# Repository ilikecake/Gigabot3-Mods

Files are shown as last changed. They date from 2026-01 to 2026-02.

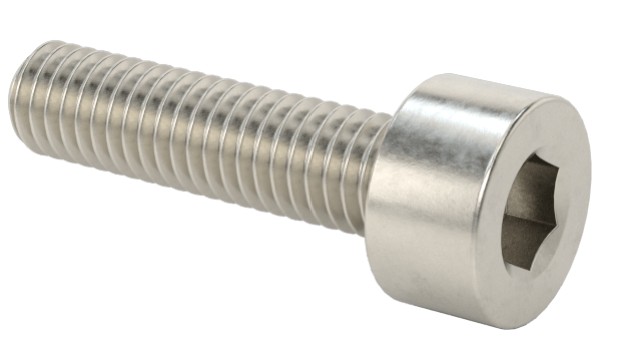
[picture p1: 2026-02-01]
Optical Endstop/M3_SHCS.jpg

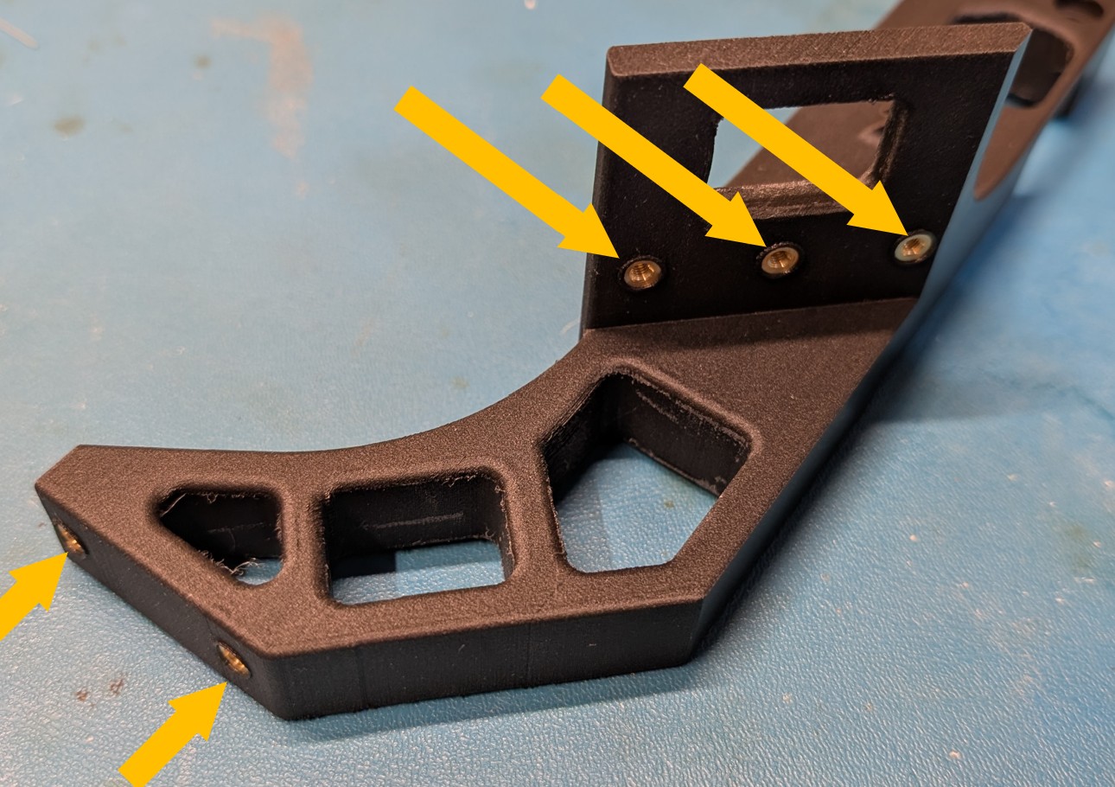
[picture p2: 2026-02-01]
XY Upright/Install_heatset.jpg

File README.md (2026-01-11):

# Gigabot 3 Mods
This repo is here to document modifications I made to the Gigabot XLT 3+. More details on the mods can be found in the Wiki.

## Background

My work purchased this [Gigabot XLT 3+](https://shop.re3d.org/pages/gigabot-xlt-3-tech-specs) a while back, looking for large format printing capability. While we did get some good prints from this printer, I found it to be pretty unreliable. As time went on, it got worse and for the last few years, it has been sitting broken in the basement of my workplace. They eventually decided to cut their losses and get rid of the printer, so I took it home. This repo documents my efforts to get the printer running again and hopefully fix some of the issues we found.

## Wishlist

Here is a list of the various things I hope to do with this printer.

Required:
- [x] Get the printer running with an upgraded firmware.
- [ ] Add a bed sensor for auto bed leveling.
- [ ] Replace the X and Y motor mounts with machined versions.
- [ ] Rebuild the print head.
- [ ] Move the thermocouple amplifier for the bed thermocouple to avoid interference with the AC bed heater.

Optional:
- [ ] Update Y endstops to optical sensors.
- [ ] Replace motor drivers with more modern variants.

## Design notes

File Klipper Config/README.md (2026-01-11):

# Klipper configuration files

 - base-config.cfg:		A basic klipper configuration that should work with the stock Gigabot XLT 3+.

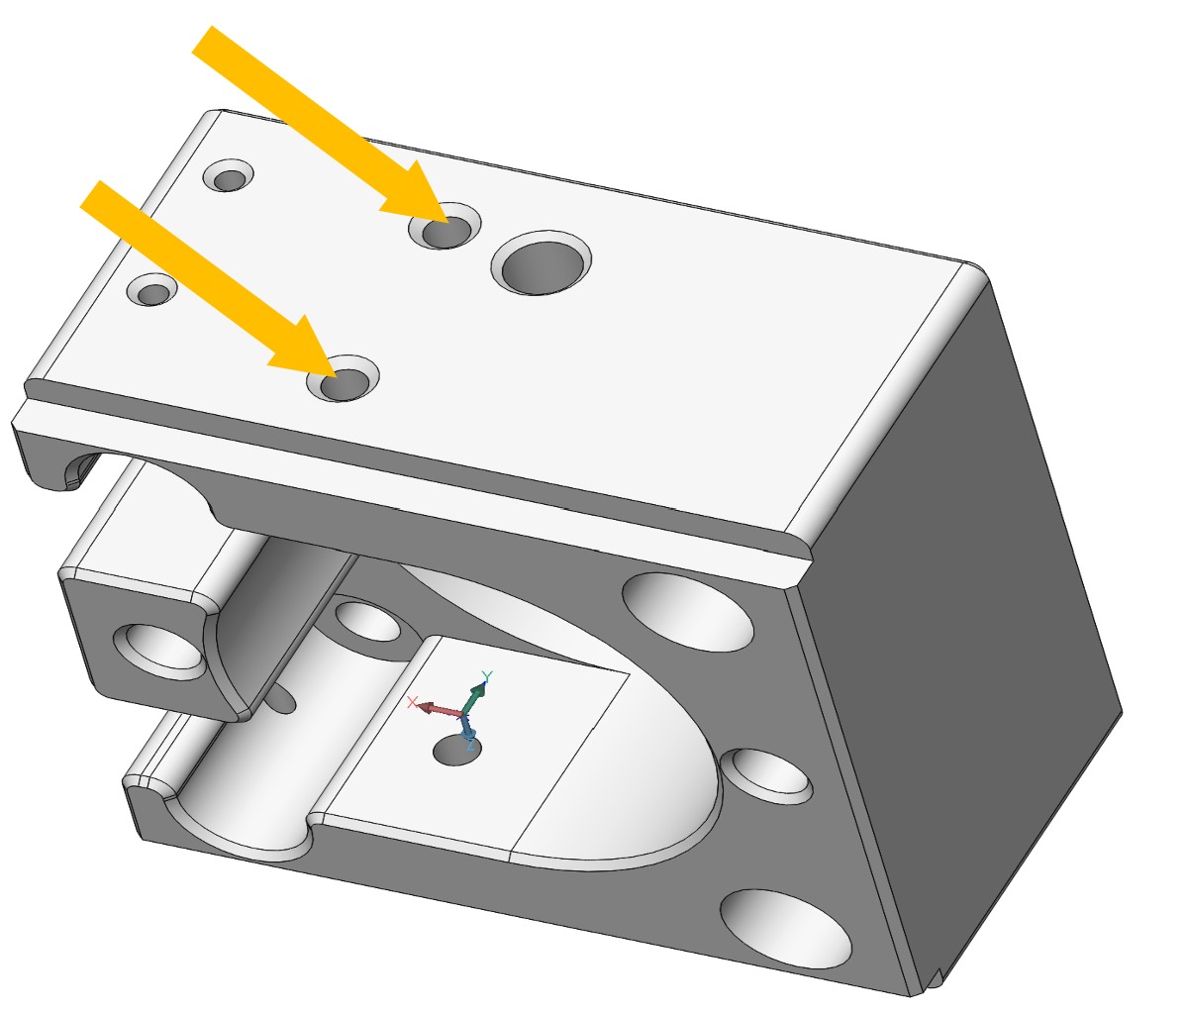
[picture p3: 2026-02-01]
Optical Endstop/Motor_mount_tap_M3.jpg

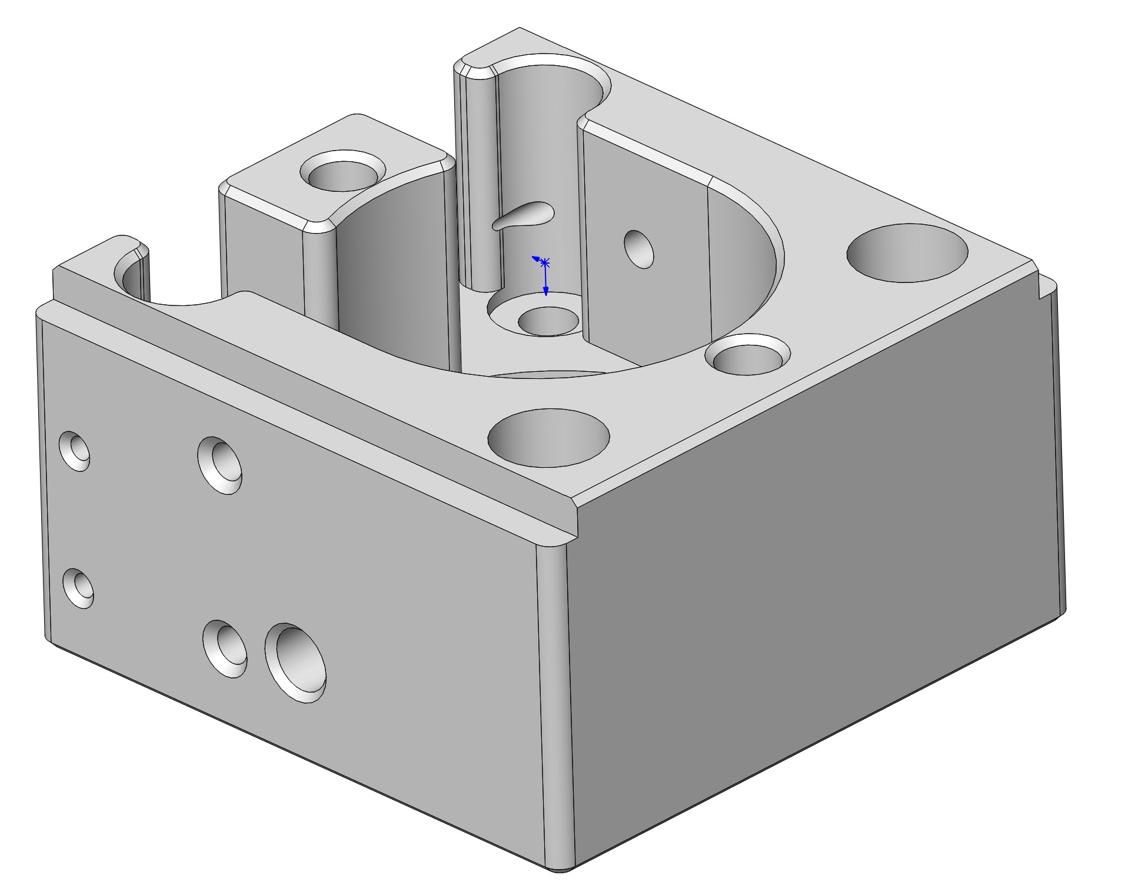
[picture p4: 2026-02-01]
Optical Endstop/Motor_mount_cad.jpg

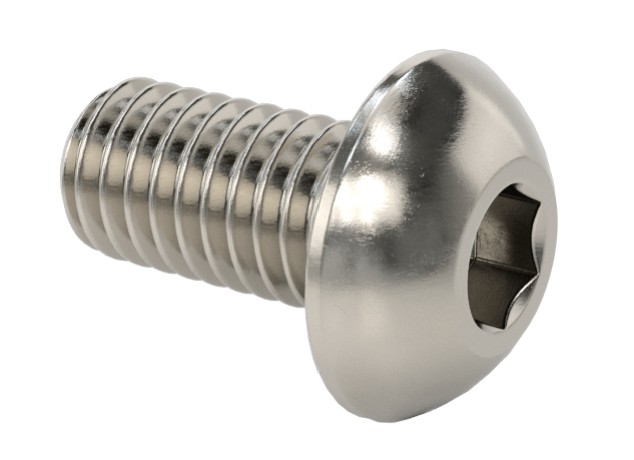
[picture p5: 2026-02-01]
Optical Endstop/M3_BHCS.jpg

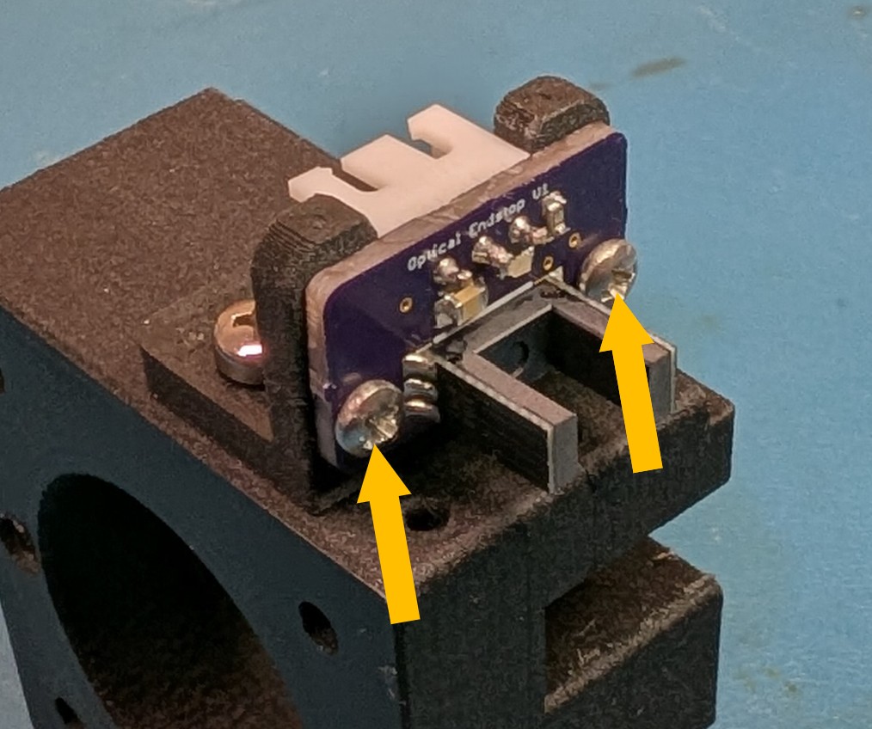
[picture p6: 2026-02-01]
Optical Endstop/PCB_to_mount.jpg

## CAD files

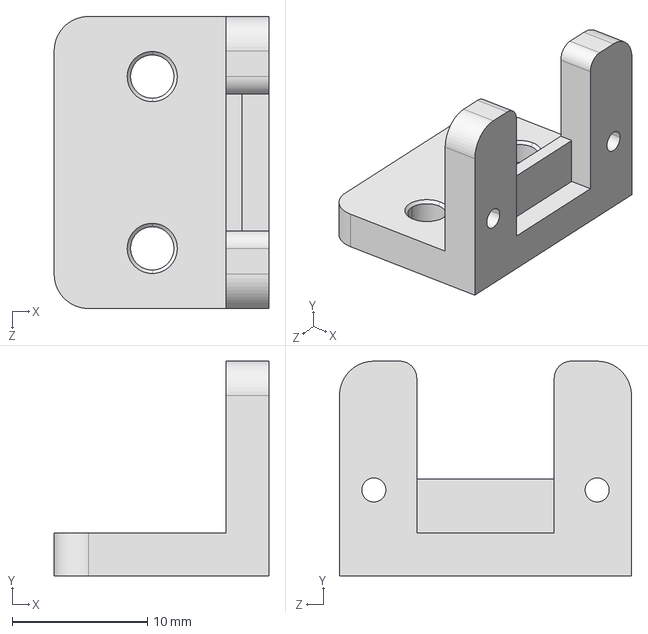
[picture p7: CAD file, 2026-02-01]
Optical Endstop/XY Optical Endstop Mount.STEP
15.9 x 15.9 x 21.6 mm

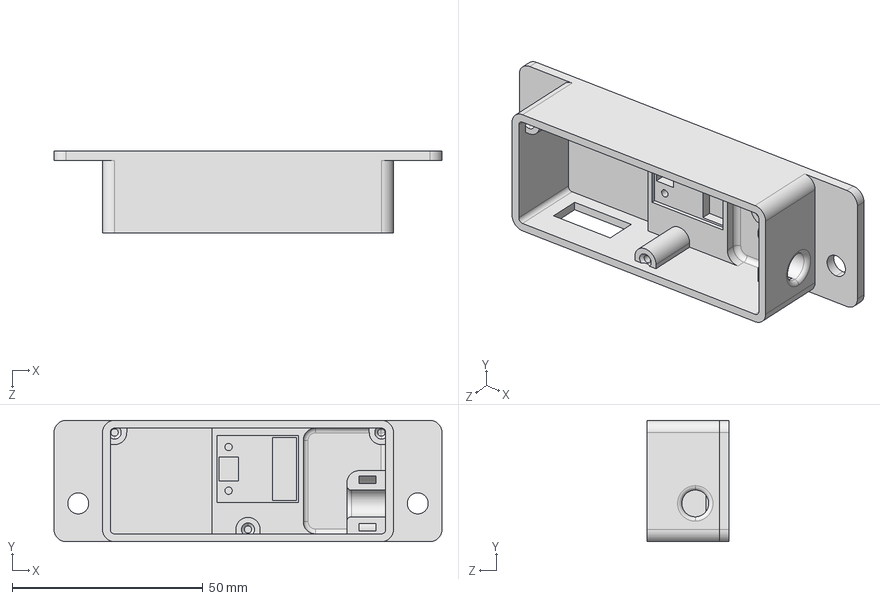
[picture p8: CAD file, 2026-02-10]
Thermocouple Amp/Thermocouple Conditioner Case.STEP
101.6 x 31.8 x 21.6 mm

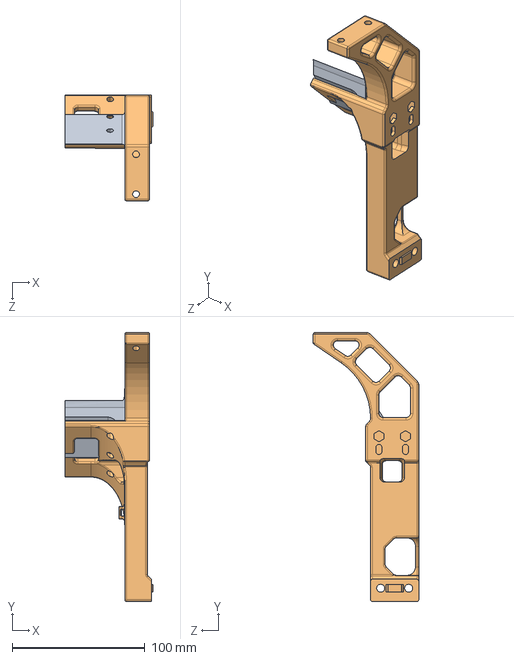
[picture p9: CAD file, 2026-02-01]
XY Upright/GB3+ XY Upright - Modified.STEP
66.3 x 202.5 x 79.5 mm

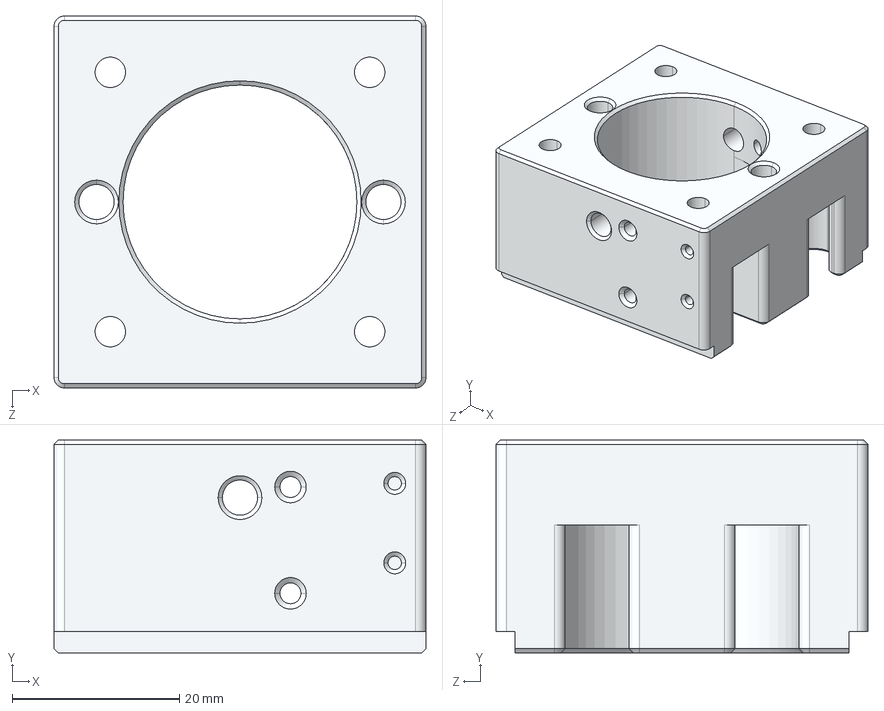
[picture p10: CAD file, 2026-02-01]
Optical Endstop/Motor Mount - Modified.STEP
44.4 x 25.4 x 44.5 mm

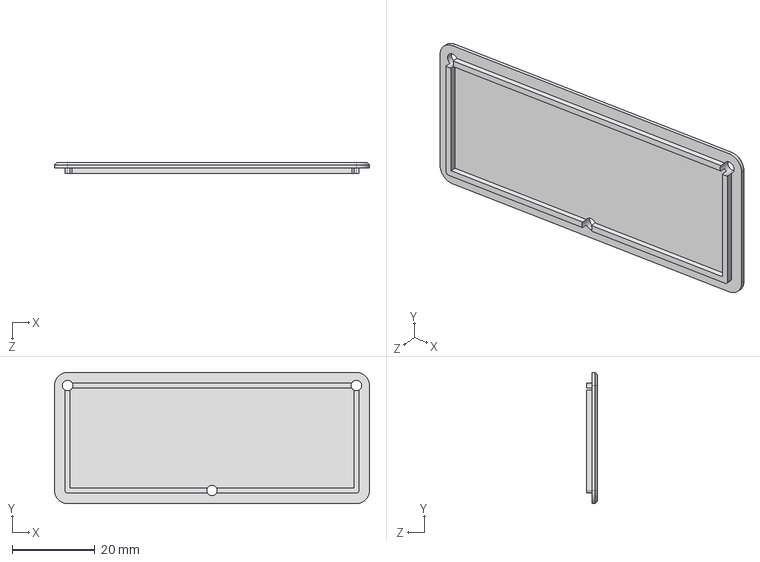
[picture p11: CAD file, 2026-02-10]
Thermocouple Amp/Thermocouple Conditioner Case Top.STEP
76.2 x 31.8 x 2.54 mm

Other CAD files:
Optical Endstop/Motor Mount - Modified.SLDPRT
Optical Endstop/Motor Mount - Modified.STL
Optical Endstop/XY Optical Endstop Mount.SLDPRT
Optical Endstop/XY Optical Endstop Mount.STL
Thermocouple Amp/Thermocouple Conditioner Case Top.SLDPRT
Thermocouple Amp/Thermocouple Conditioner Case Top.STL
Thermocouple Amp/Thermocouple Conditioner Case.SLDPRT
Thermocouple Amp/Thermocouple Conditioner Case.STL
XY Upright/GB3+ XY Upright - Modified.SLDPRT

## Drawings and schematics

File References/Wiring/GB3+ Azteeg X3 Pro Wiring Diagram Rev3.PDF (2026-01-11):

# + AZTEEG

# + ELECTRICAL BOX FANS

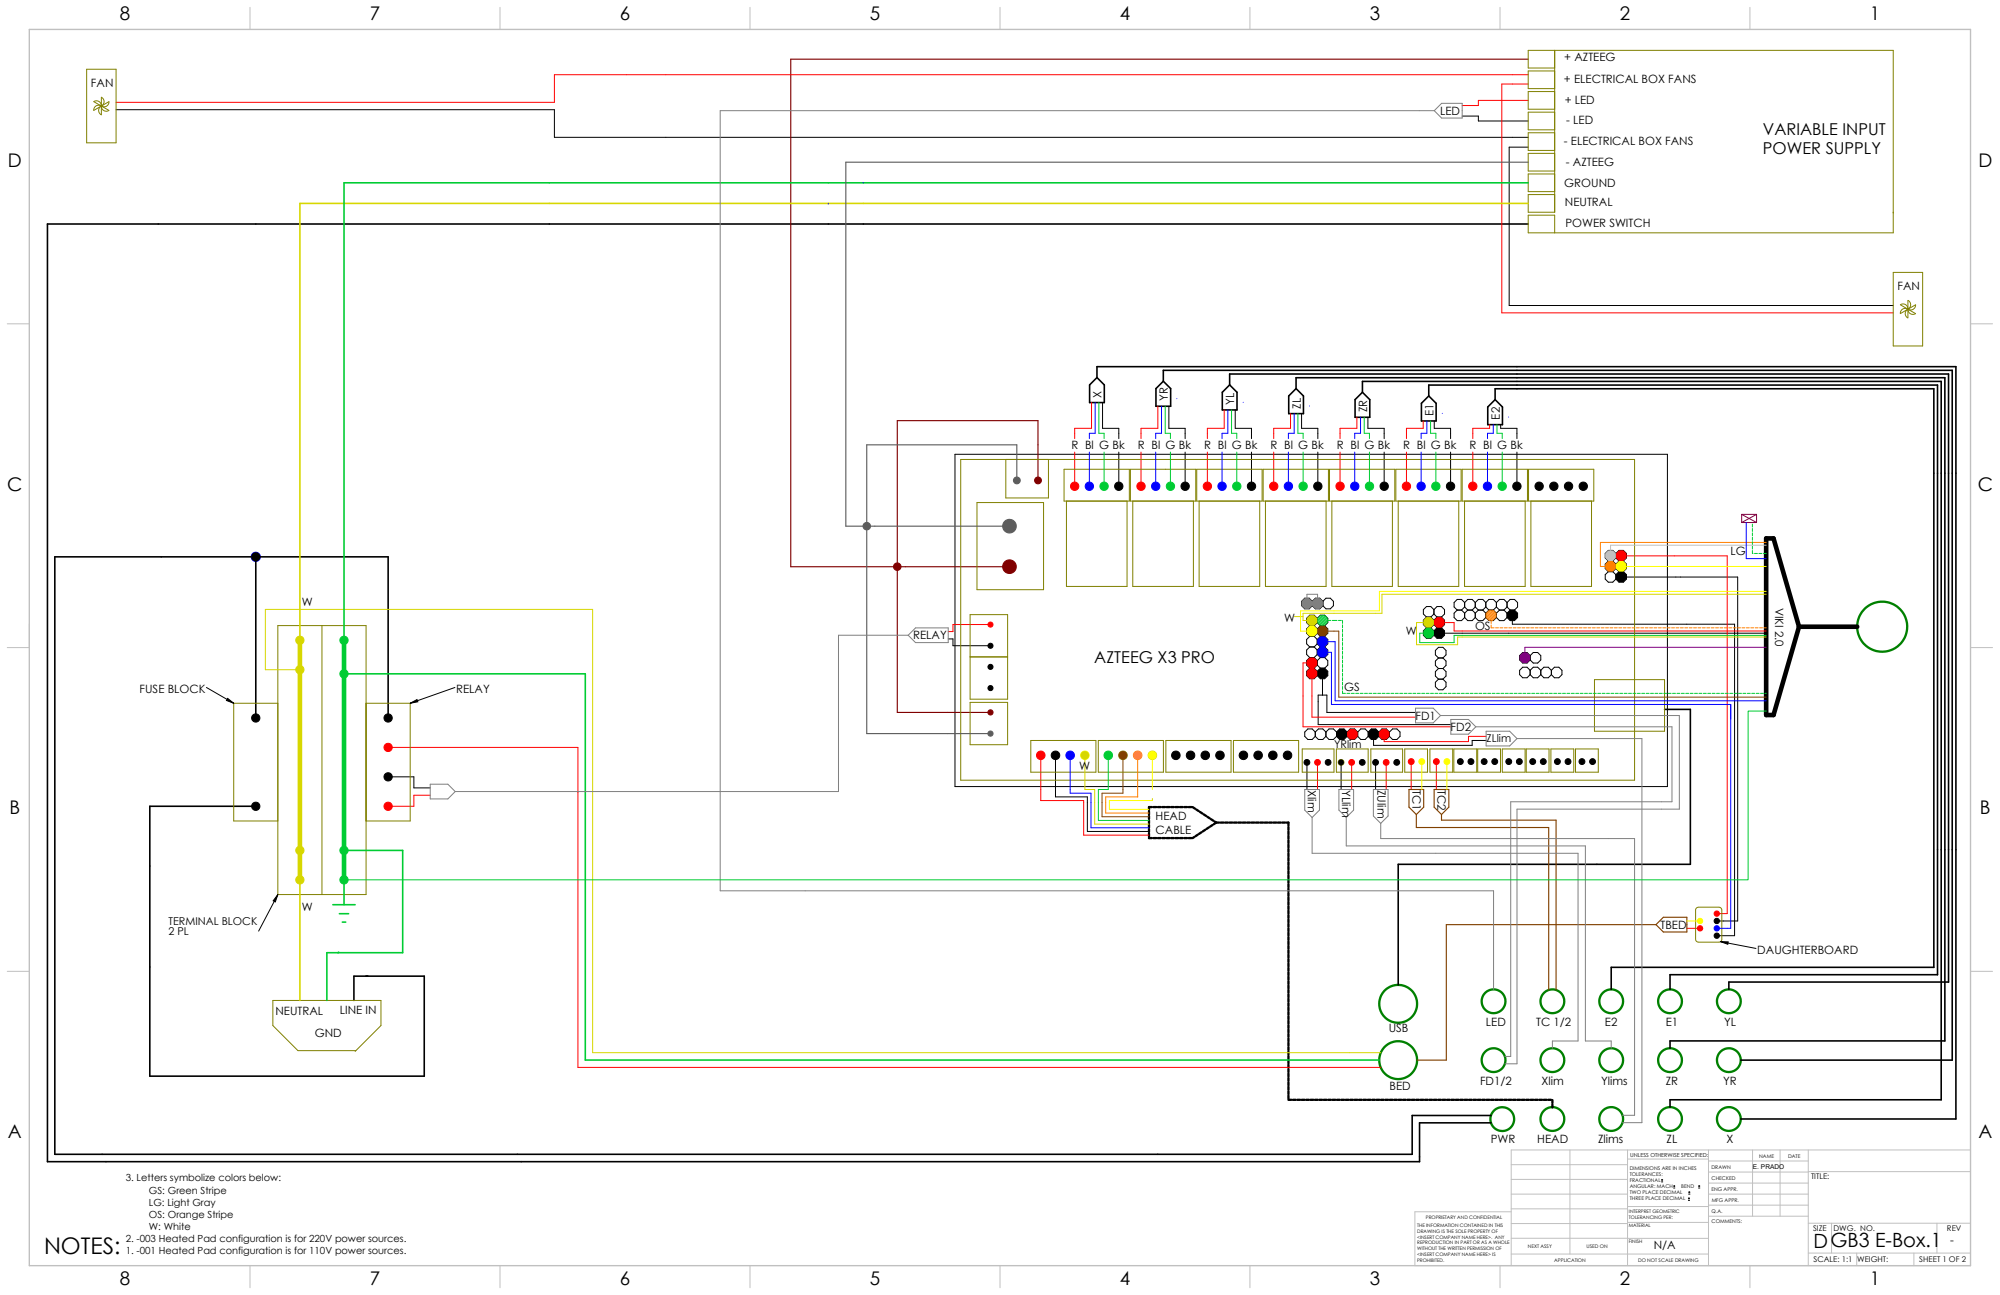
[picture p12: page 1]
HEAD; USB; BED; PWR; LED; Zlims; Xlim; Ylims; Ulim; ZLlim; + LED - LED; - ELECTRICAL BOX FANS; - AZTEEG; GROUND NEUTRAL; POWER SWITCH; GND; LINE IN; FAN; VIKI 2.0; HEAD CABLE; Llim; FUSE BLOCK; RELAY; VARIABLE INPUT POWER SUPPLY; AZTEEG X3 PRO; TERMINAL BLOCK 2 PL; TBED; DAUGHTERBOARD; NEUTRAL; NOTES:; YRlim; COMMENTS:

UNLESS OTHERWISE SPECIFIED: | | NAME | DATE
DIMENSIONS ARE IN INCHES TOLERANCES: FRACTIONAL ANGULAR: MACH BEND TWO PLACE DECIMAL THREE PLACE DECIMAL | DRAWN | E. PRADO

3. Letters symbolize colors below:
GS: Green Stripe
LG: Light Gray
OS: Orange Stripe
W: White
2. -003 Heated Pad configuration is for 220V power sources.
1. -001 Heated Pad configuration is for 110V power sources.

CHECKED | | | TITLE:

ENG APPR.
MFG APPR.

INTERPRET GEOMETRIC TOLERANCING PER: | Q.A.
MATERIAL | | SIZE D | DWG. NO. GB3 E-Box.1 | REV -

PROPRIETARY AND CONFIDENTIAL
THE INFORMATION CONTAINED IN THIS
DRAWING IS THE SOLE PROPERTY OF
<INSERT COMPANY NAME HERE>. ANY
REPRODUCTION IN PART OR AS A WHOLE
WITHOUT THE WRITTEN PERMISSION OF
<INSERT COMPANY NAME HERE> IS
PROHIBITED.

NEXT ASSY | USED ON | FINISH N/A

APPLICATION | DO NOT SCALE DRAWING | | SCALE: 1:1 | WEIGHT: | SHEET 1 OF 2

YL

E2 | E1

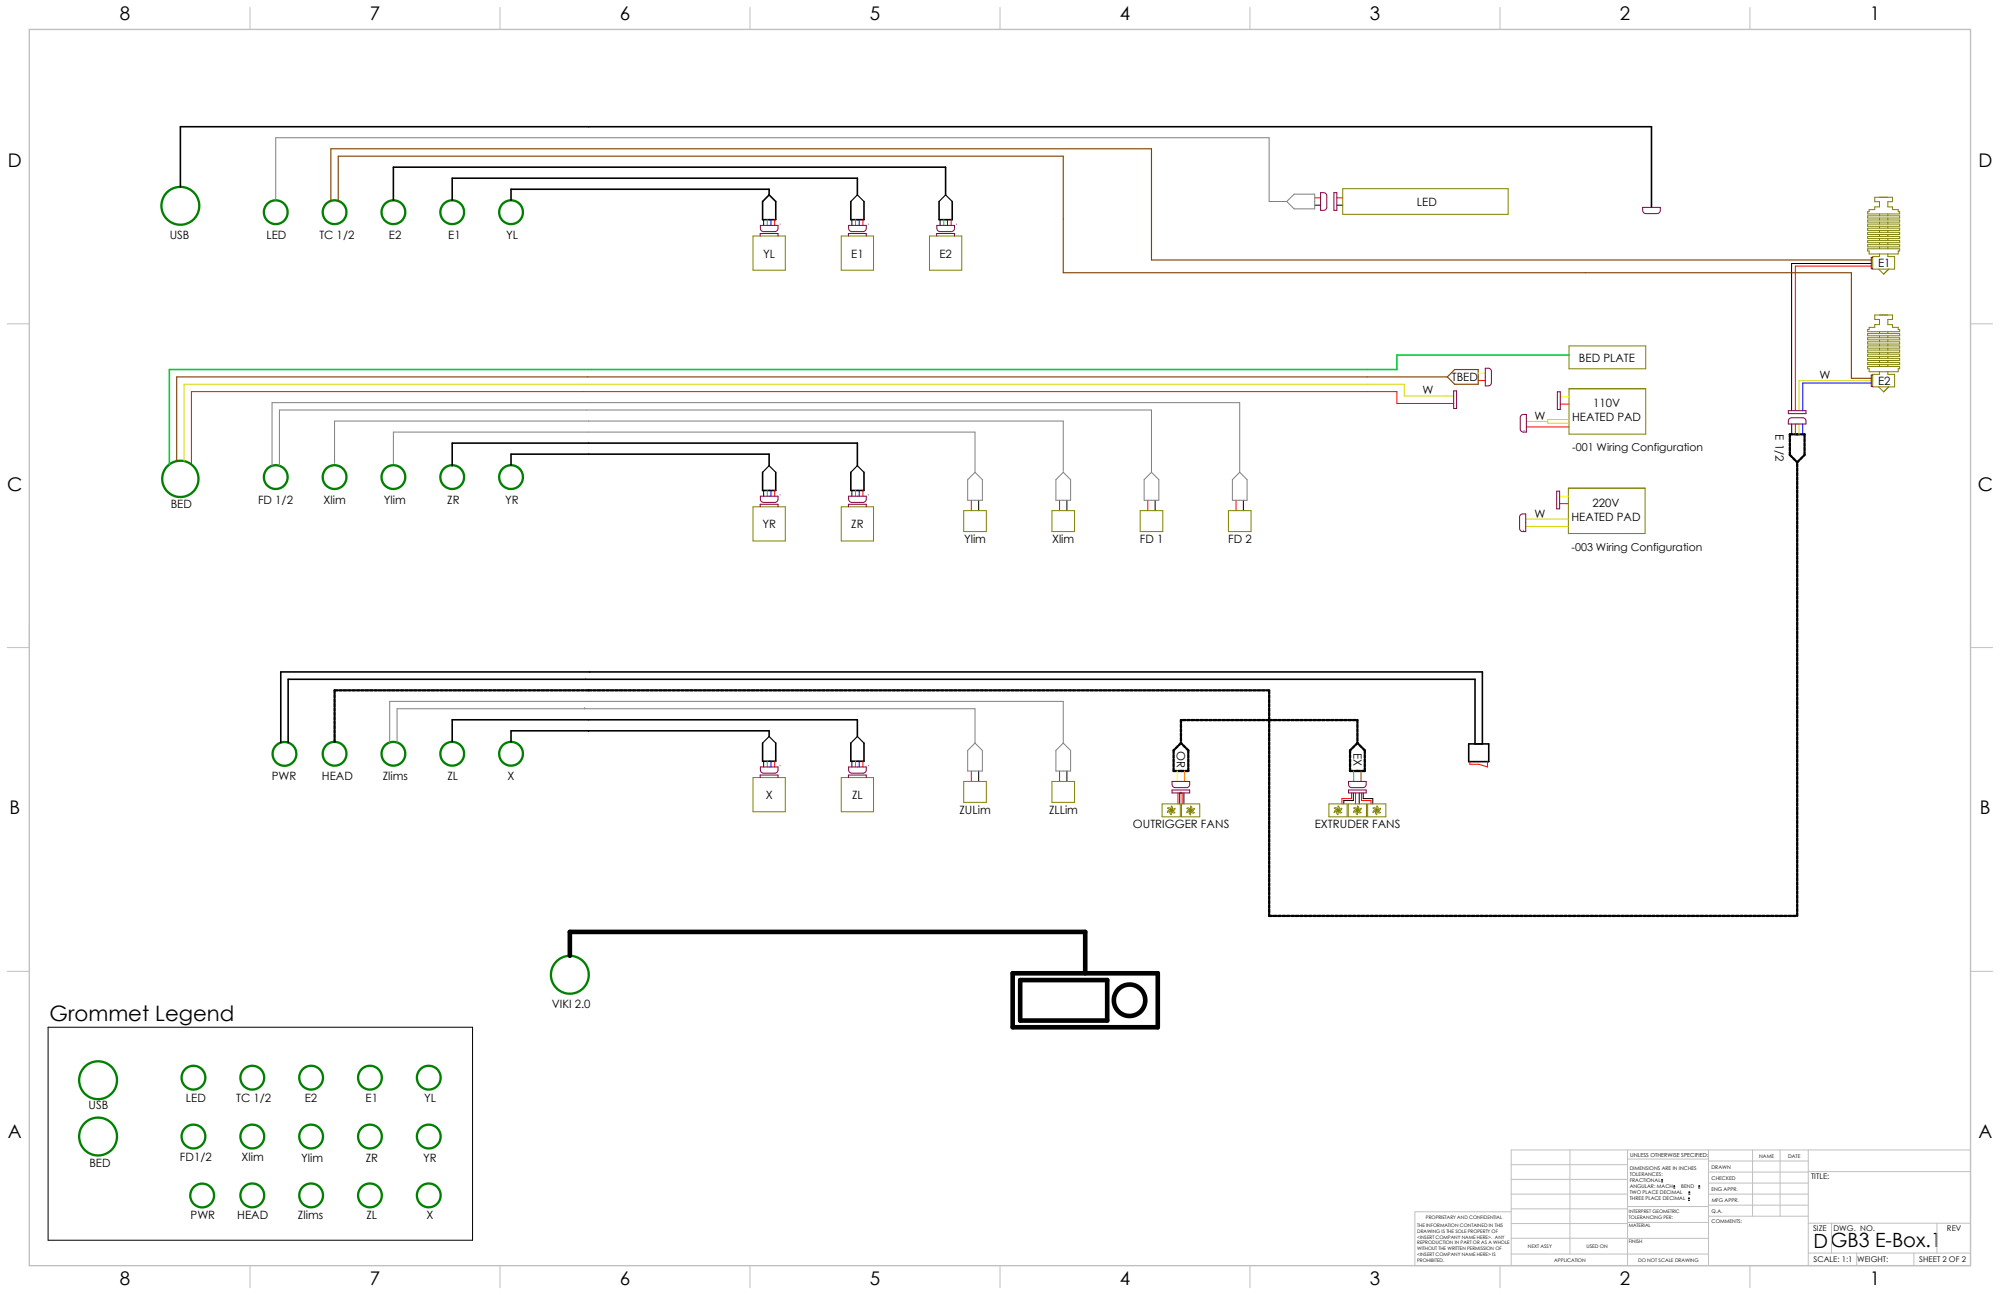
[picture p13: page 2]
HEAD; ZR BED; USB; PWR; LED; Zlims; Xlim; Ylim; BED PLATE; 110V HEATED PAD; VIKI 2.0; OUTRIGGER FANS; EXTRUDER FANS; ZULim; ZLLim; TBED; 220V HEATED PAD; -001 Wiring Configuration; -003 Wiring Configuration; BED; Grommet Legend; COMMENTS:

UNLESS OTHERWISE SPECIFIED: | | NAME | DATE

DIMENSIONS ARE IN INCHES TOLERANCES: FRACTIONAL ANGULAR: MACH BEND TWO PLACE DECIMAL THREE PLACE DECIMAL | DRAWN

CHECKED | | | TITLE:

ENG APPR.
MFG APPR.

INTERPRET GEOMETRIC TOLERANCING PER: | Q.A.
MATERIAL | | SIZE D | DWG. NO. GB3 E-Box.1 | REV

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

NEXT ASSY | USED ON | FINISH

APPLICATION | DO NOT SCALE DRAWING | | SCALE: 1:1 | WEIGHT: | SHEET 2 OF 2

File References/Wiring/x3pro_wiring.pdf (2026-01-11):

### X-AXIS Y-AXIS Z-AXIS EXTR1

## STEPPER MOTORS

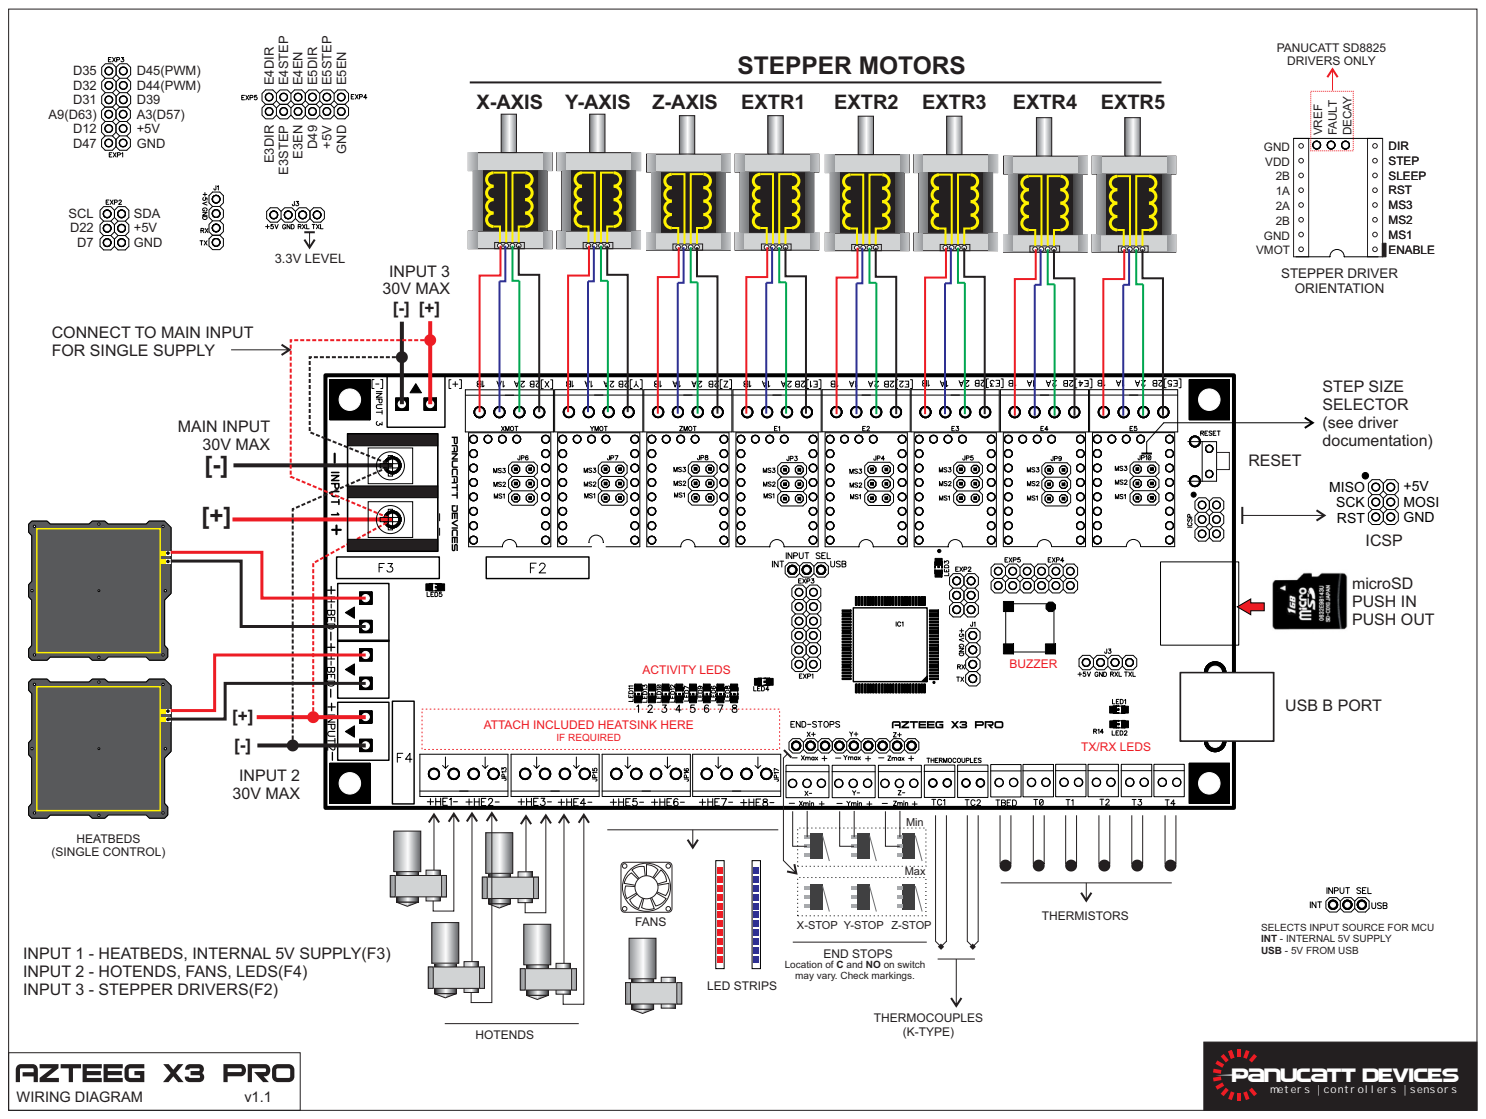
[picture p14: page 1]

CONNECT TO MAIN INPUT
FOR SINGLE SUPPLY

ATTACH INCLUDED HEATSINK HERE

SELECTS INPUT SOURCE FOR MCU
INT - INTERNAL 5V SUPPLY
USB - 5V FROM USB

INPUT 1 - HEATBEDS, INTERNAL 5V SUPPLY(F3)
INPUT 2 - HOTENDS, FANS, LEDS(F4)
INPUT 3 - STEPPER DRIVERS(F2)

Location of C and NO on switch
may vary. Check markings.

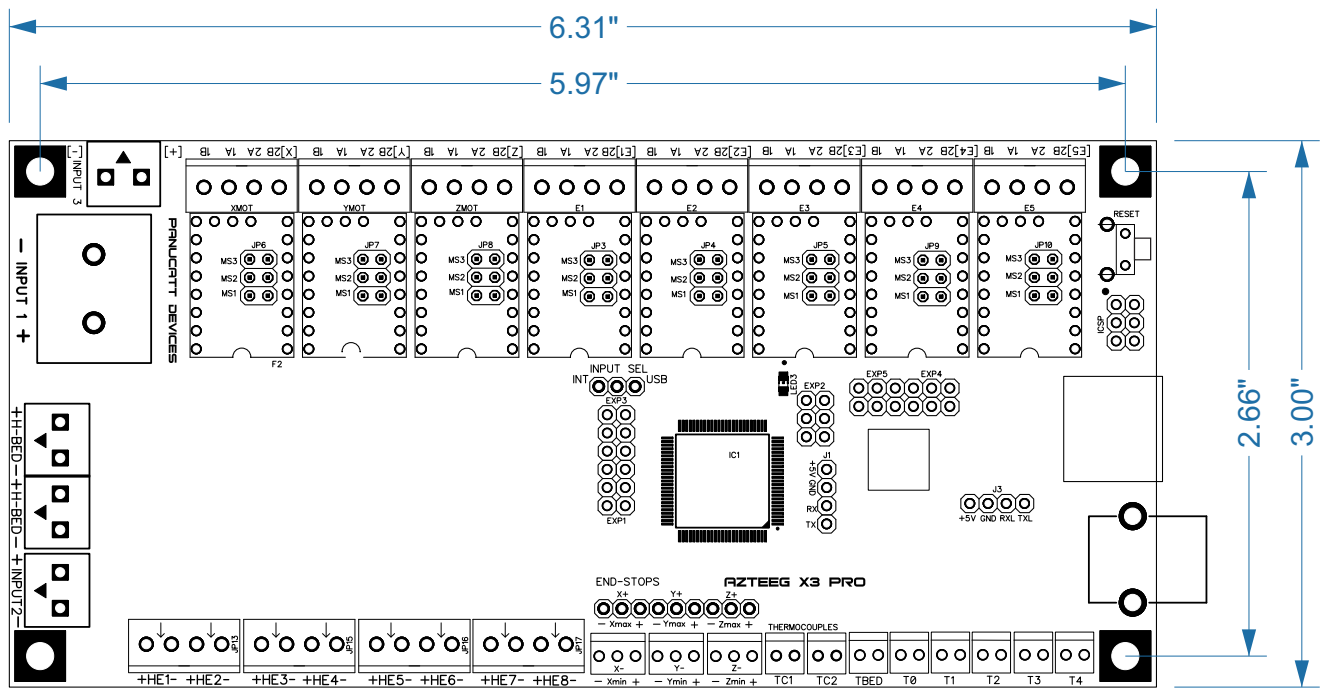
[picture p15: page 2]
WIRING DIAGRAM; PANUCATT DEVICES

meters | controllers | sensors

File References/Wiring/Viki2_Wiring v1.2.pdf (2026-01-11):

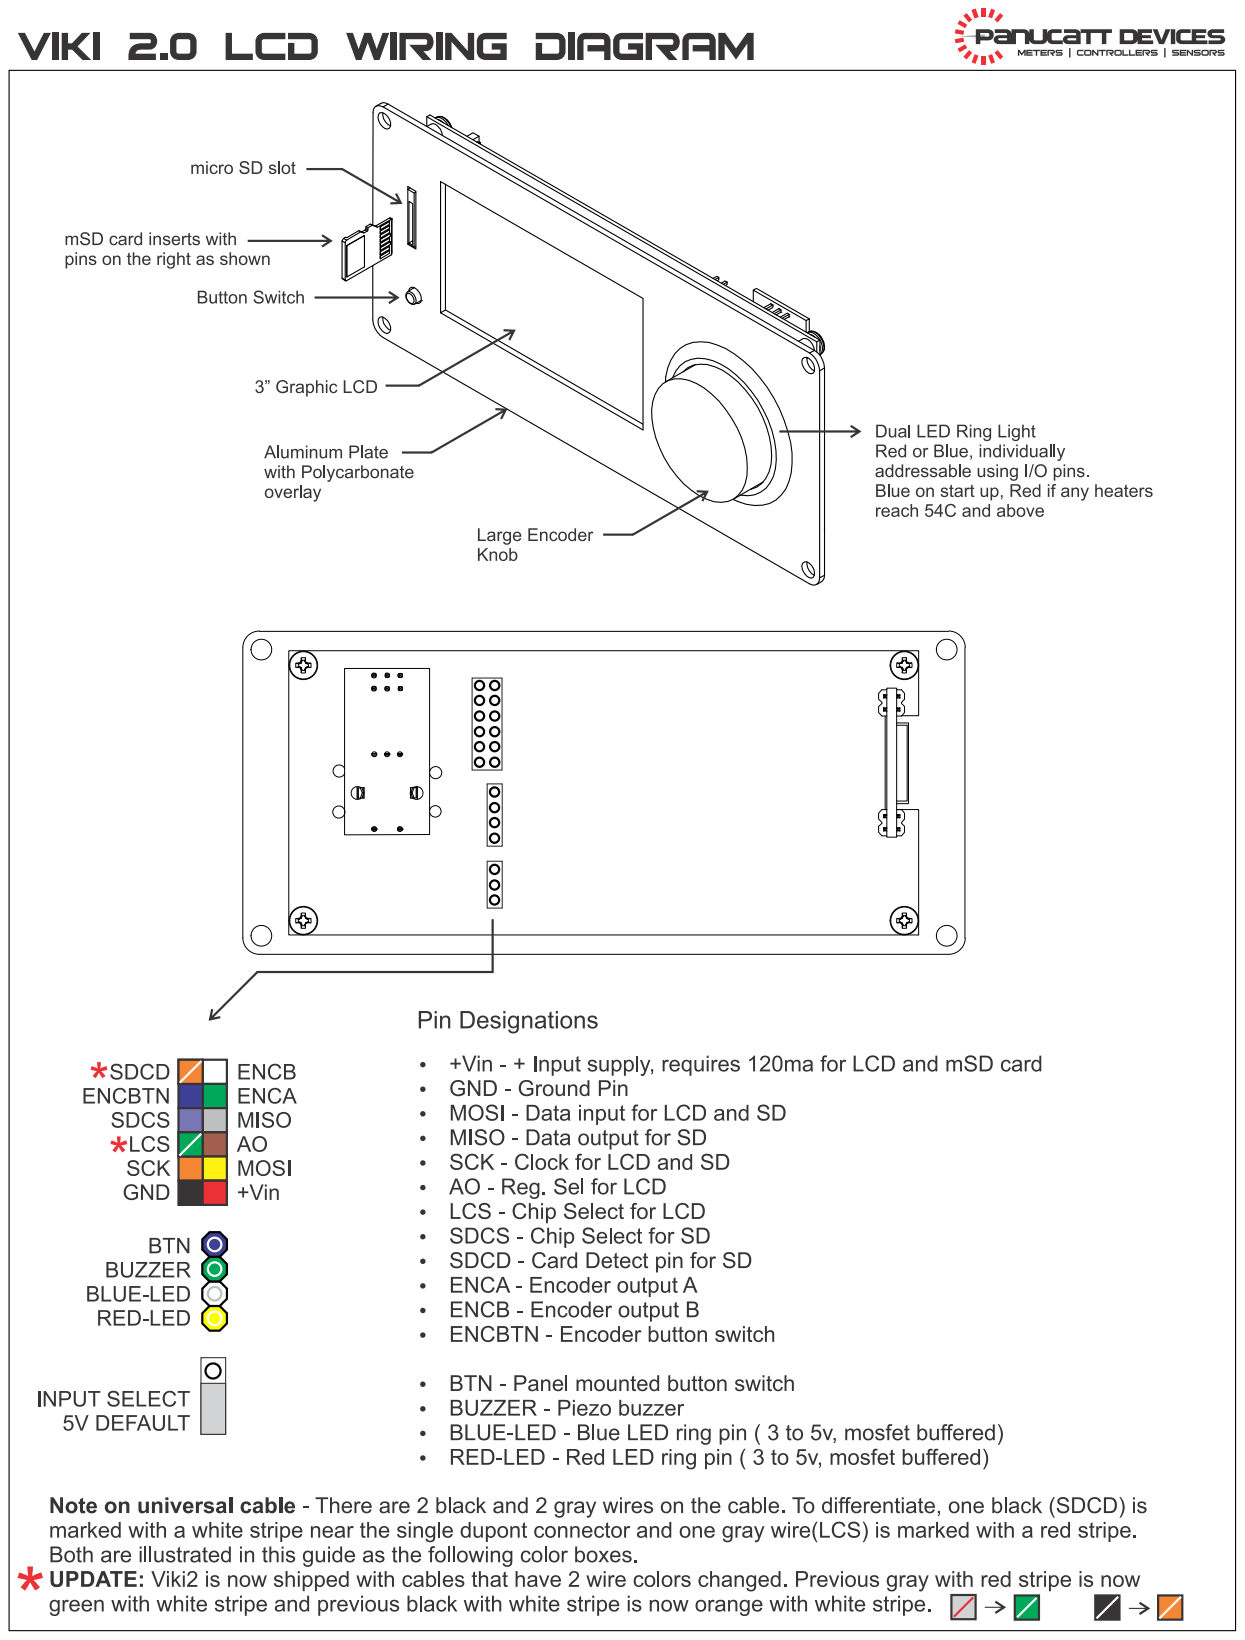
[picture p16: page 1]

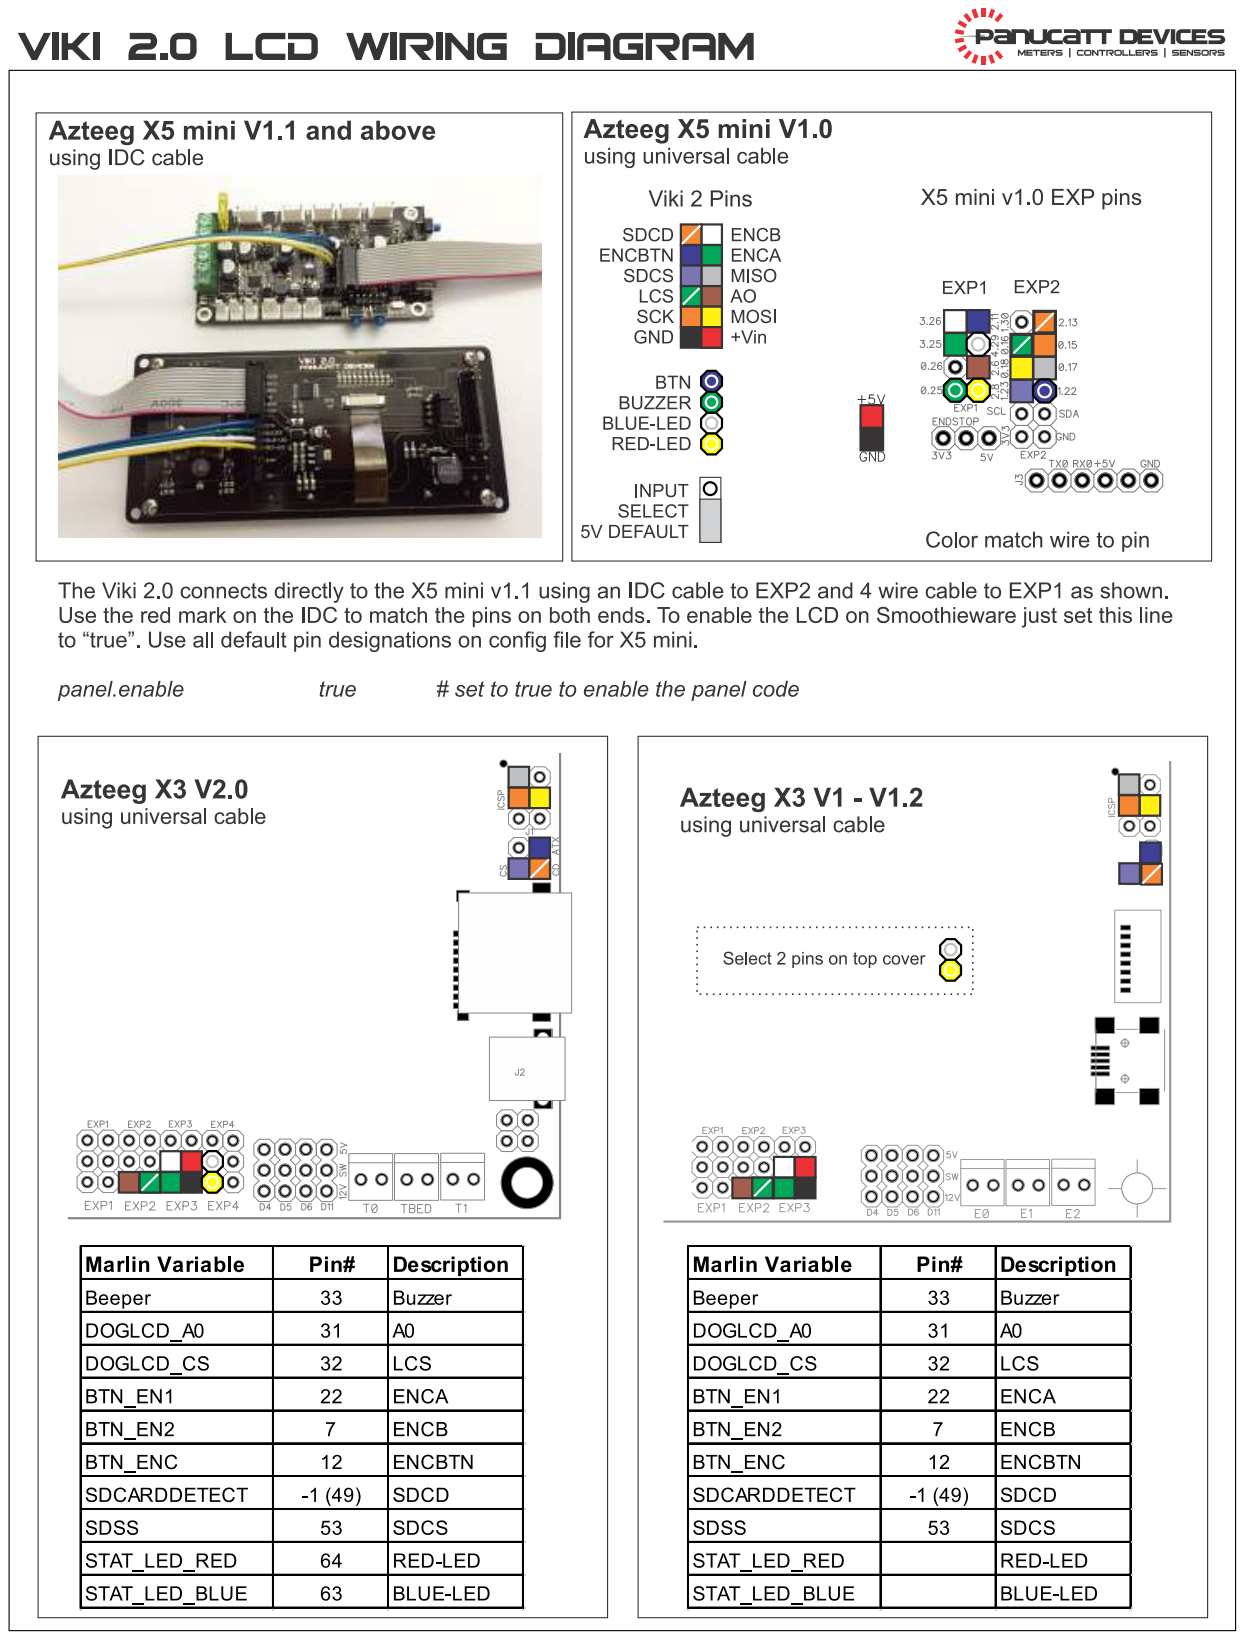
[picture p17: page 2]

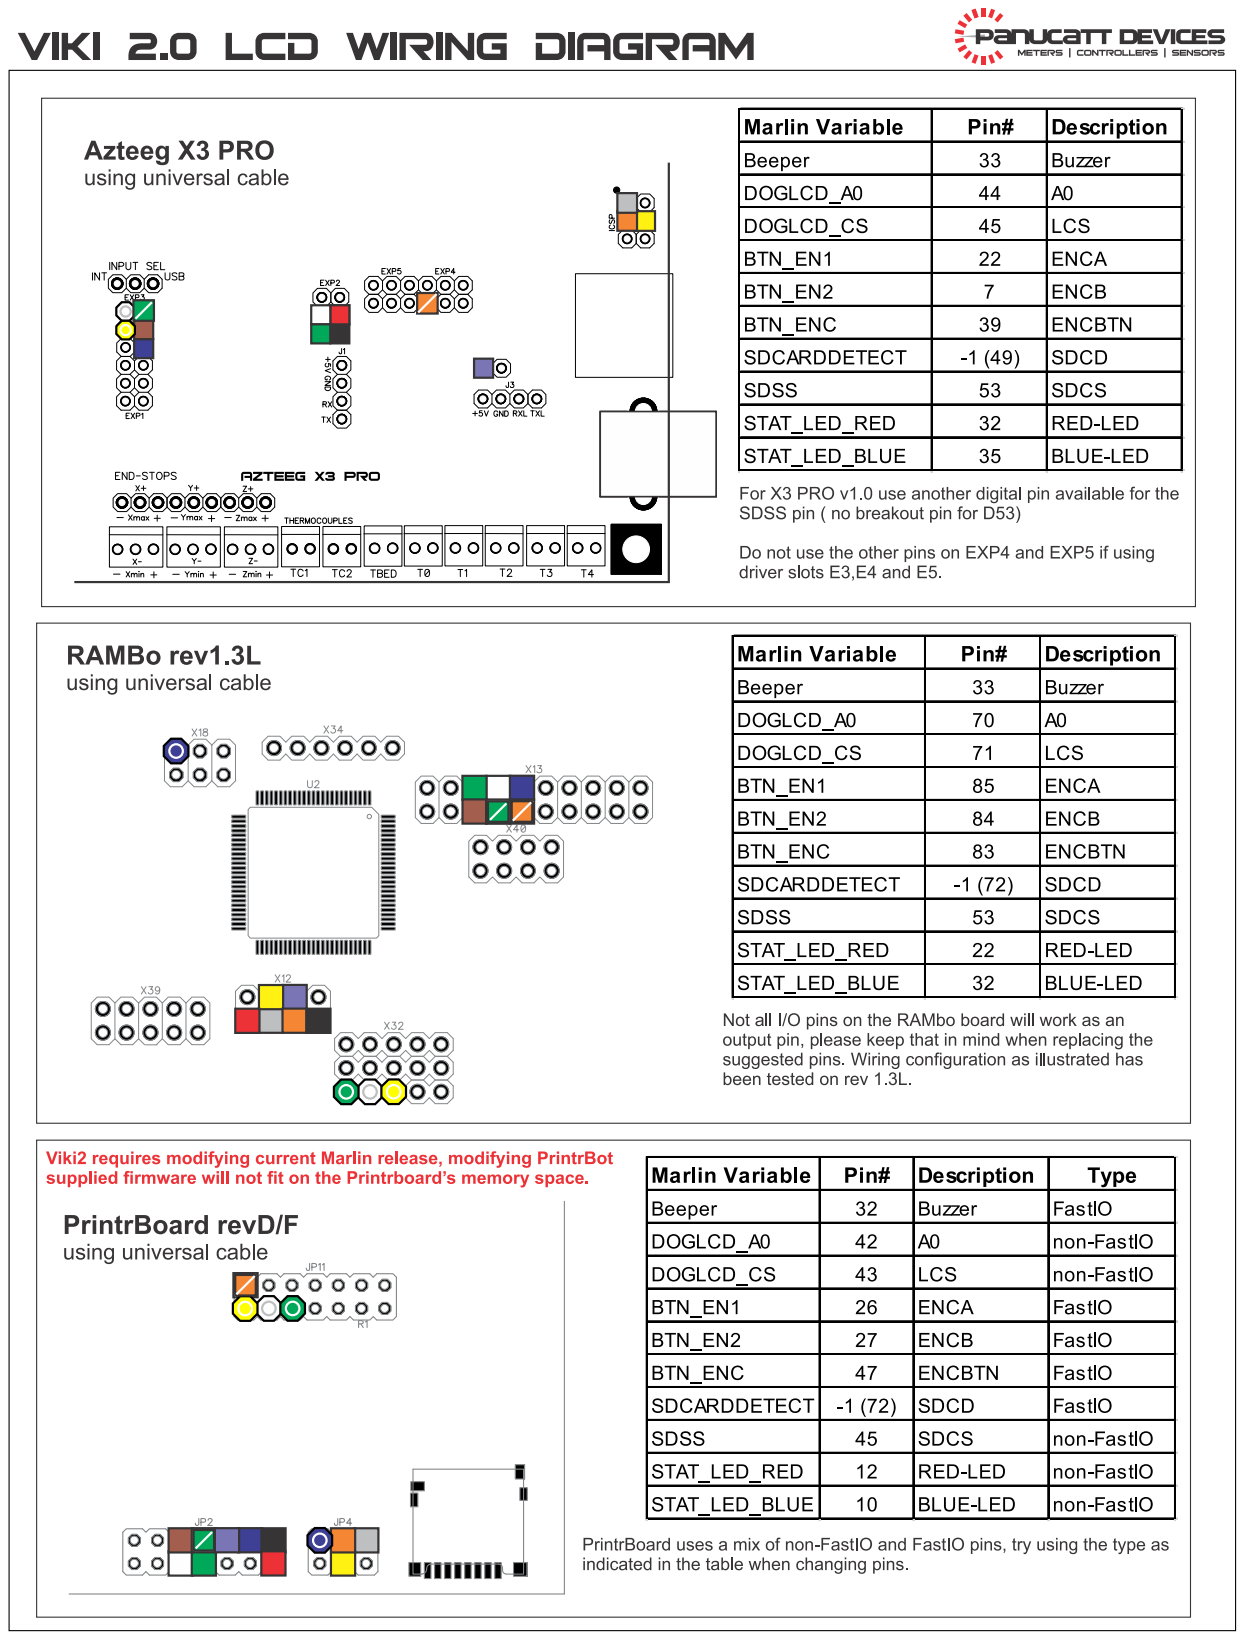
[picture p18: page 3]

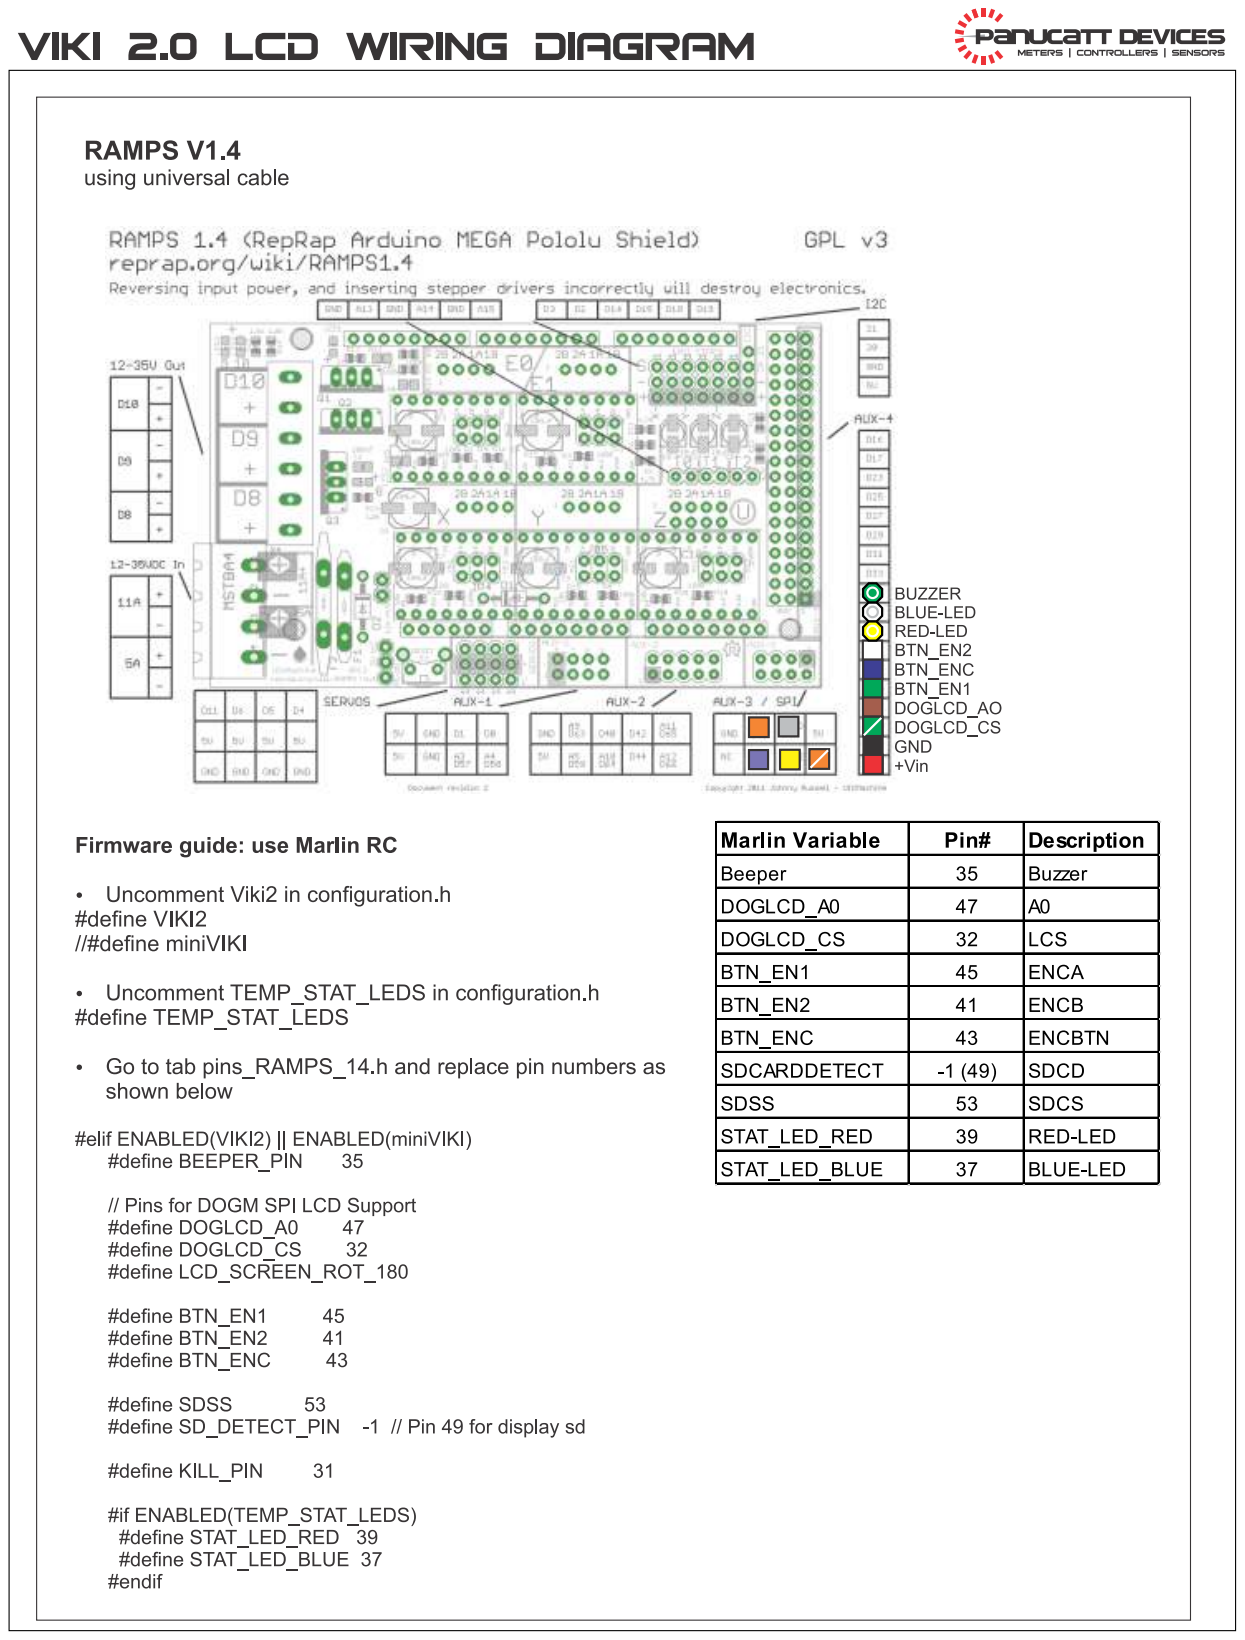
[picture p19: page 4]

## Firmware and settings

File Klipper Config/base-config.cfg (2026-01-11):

# This file contains common pin mappings for the Gigabot XLT 3+.
# Azteeg X3 Pro board uses a firmware compiled for the AVR
# atmega2560.
#
# ! = inverted pin (active low)
# ^ = pull up enabled
# ~ = pull down enabled
#
# See docs/Config_Reference.md for a description of parameters.
#
#  TODO:
#	
#
#  Fixed:
#	-#define INVERT_Y2_VS_Y_DIR true   // Set 'true' if Y motors should rotate in opposite directions <--- Done, test this without the belts installed incase I messed it up.
#	-#define LCD_SCREEN_ROT_180 <---- Not supported in Klipper?? (https://github.com/Klipper3d/klipper/issues/2097)
#	-AD8495 gain and offset? Set to G=2, offset=-250, formula is (5.0 * 100.0) / 1024.0 / (OVERSAMPLENR) * (TEMP_SENSOR_AD8495_GAIN) + TEMP_SENSOR_AD8495_OFFSET <-- this is from OFW, but the schematic shows the ref pin tied to ground, so that should mean an offset of 0v.
#	-AD595 gain? Set to 2 in OFW <--- this is in the OFW, but I don't see an AD595 on the schematic
#   -Case Light? <-- Case light is directly connected to 12V
#   -Z Max?? <--- doesnt seem possible in Klipper??
#	-Three jumpers for the driver mean 1/32 microstepping. This will affect the microsteps and full steps per rotation settings. <-- Changed microsteps and rotation distance for all steppers.
#	-Drivers are DRV8825 chip on a SD8825 board. Does this require changes? <-- just the microsteps and rotation distance from above.
#
#  Notes
#	-Verified by inspection: all steppers have all three jumpers installed.
#
#
#Flashing the MCU.
# -SSH into your device running Klipper (Raspberry Pi, etc...)
# -Determine the port ID using these instructions: 
#  https://www.klipper3d.org/FAQ.html#wheres-my-serial-port
# -Make sure your locale is set correctly on your device running
#  klipper. For my Rasperry Pi, I needed to run `sudo raspi-config`
#  and set the locale in `localisation options`.
# -Run `make menuconfig` to open the menu to set MCU settings.
#  - Micro-controller Architecture: Atmega AVR
#  - Processor model: atmega2560 
# -run `make` to build the MCU firmware.
# -Stop the Klipper service: `sudo service klipper stop`
# -Flash the MCU: `make flash FLASH_DEVICE=<your port ID>`.
# -Check the output of avrdude to make sure the flash was successful.
# -Start Klipper again: ` sudo service klipper start`
#



[include mainsail.cfg]

[mcu]
 serial: /dev/serial/by-id/usb-FTDI_FT231X_USB_UART_DN04GSGV-if00-port0

[printer]
 #Max velocities from OFW.
 kinematics: cartesian
 max_velocity: 150
 max_accel: 2000
 max_z_velocity: 10
 max_z_accel: 100

[stepper_x]
 step_pin: x_step
 dir_pin: !x_dir
 enable_pin: !x_enable
 microsteps: 32						#Three jumpers are installed, with DRV8825 drivers, this means 32 microsteps.
 full_steps_per_rotation: 200		#default, not needed
 rotation_distance: 54				#From the marlin output
 endstop_pin: ^!x_min_endstop   	#Endstops are grounded when triggered. Pullup required.
 position_endstop: 0
 position_max: 590
 homing_speed: 20

[stepper_y]
 #This is the stepper and endstop labeled YR
 step_pin: y_step
 dir_pin: !y_dir
 enable_pin: !y_enable
 microsteps: 32
 full_steps_per_rotation: 200		#default, not needed
 rotation_distance: 54
 endstop_pin: ^!y_max_endstop
 position_endstop: 0
 position_max: 760
 homing_speed: 20
 
[stepper_y1]
 #This is the stepper and endstop labeled YL
 step_pin: z_step
 dir_pin: z_dir						#This is inverted from stepper_y because the second Y motor needs to rotate the opposite way from the first.
 enable_pin: !z_enable
 microsteps: 32
 full_steps_per_rotation: 200		#default, not needed
 rotation_distance: 54
 endstop_pin: ^!y_min_endstop
 #position_endstop: 0
 #position_max: 760
 #homing_speed: 5
 
[stepper_z]
 #This is the stepper and endstop labeled ZL
 step_pin: e1_step
 dir_pin: e1_dir
 enable_pin: !e1_enable
 microsteps: 32
 full_steps_per_rotation: 200		#default, not needed
 rotation_distance: 1.5875			#From Marlin, might need to check this. The threaded rod is labeled .375-8 ACME in CAD
 endstop_pin: ^!PD3
 position_endstop: 0
 position_max: 900
 position_min: 0.0
 homing_speed: 5
 
[stepper_z1]
 #This is the stepper labeled ZR
 step_pin: e2_step
 dir_pin: e2_dir
 enable_pin: !e2_enable
 microsteps: 32
 full_steps_per_rotation: 200		#default, not needed
 rotation_distance: 1.5875			#From Marlin, might need to check this. The threaded rod is labeled .375-8 ACME in CAD
 #endstop_pin: ^PD3					#There is only 1 Z endstop
 #position_endstop: 0
 #position_max: 900
 #position_min: 0.0
 
[extruder]
 step_pin: e3_step
 dir_pin: !e3_dir
 enable_pin: !e3_enable
 microsteps: 32
 rotation_distance: 6.4				#From OFW, may need to be calibrated
 nozzle_diameter: 0.4
 filament_diameter: 2.85
 max_extrude_only_distance: 20000	#From Re3D firmware. This seems a bit long.
 heater_pin: hotend_1				#Red and black
 sensor_type: AD8495				#JD3 header is TC1
 sensor_pin: thermocouple1
 min_temp: 0
 max_temp: 250
 control: pid
 pid_kp: 16.533						#Calibrated values from my machine. Should be an okay starting point, but run your own cal.
 pid_ki: 0.538
 pid_kd: 127.100

[extruder1]
 step_pin: e4_step
 dir_pin: e4_dir
 enable_pin: !e4_enable
 microsteps: 32
 rotation_distance: 6.4				#From OFW, may need to be calibrated
 nozzle_diameter: 0.4
 filament_diameter: 2.85
 max_extrude_only_distance: 20000	#From OFW, this seems a bit long.
 heater_pin: hotend_2				#Blue and white
 sensor_type: AD8495
 sensor_pin: thermocouple2
 min_temp: 0
 max_temp: 250
 control: pid
 pid_kp: 28.151						#Calibrated values from my machine. Should be an okay starting point, but run your own cal.
 pid_ki: 1.738
 pid_kd: 114.013

[heater_bed]
 heater_pin: hotbed
 sensor_type: AD8495
 voltage_offset: -1.24
 sensor_pin: PF3
 min_temp: 0
 max_temp: 120
 control: pid
 pid_kp: 62.838					   #Calibrated values from my machine. Should be an okay starting point, but run your own cal.
 pid_ki: 1.682
 pid_kd: 586.754

[fan]
 #Part cooling fan
 pin: hotend_4

[heater_fan heatbreak_fan]
 pin: hotend_3
 heater: extruder, extruder1
 heater_temp: 50.0

[filament_switch_sensor e1_sensor]
 #Labeled FD1 in the wiring diagram
 switch_pin: ^!PL2

[filament_switch_sensor e2_sensor]
 #Labeled FD2 in the wiring diagram
 switch_pin: ^!PB6

#Pots are scaled so that the value for the wipers is the current limit in
# amps for the DRV8825 driver. The values below are derated to 90% of the 
# maximum current listed for the motors. The OFW sets these to 100% of the 
# max current of the motors, so this setting will likley result in a bit 
# less torque from the motors.
[mcp4451 pot1]
 i2c_address: 44
 wiper_0: 1.8     #Goes to X motor
 wiper_1: 1.8     #Goes to YR motor
 wiper_2: 1.8     #Goes to YL motor
 wiper_3: 1.512   #Goes to ZL motor
 scale: 2.424

[mcp4451 pot2]
 i2c_address: 46
 wiper_0: 1.512    #Goes to ZR motor
 wiper_1: 1.53     #Goes to extruder 1 motor
 wiper_2: 1.53     #Goes to extruder 2 motor
 wiper_3: 0	       #Unused
 scale: 2.413

[display]
 #The Viki2 display is actually ST7565 based, but the UC1701 type works here.
 lcd_type: uc1701
 cs_pin: viki2_lcd_cs
 a0_pin: viki2_lcd_a0
 contrast: 50
 encoder_pins: ^viki2_enc_a, ^viki2_enc_b
 click_pin: ^!viki2_enc_btn
 
[led viki_ring_led]
 red_pin: PC5
 blue_pin: PC2
 
[output_pin buzzer_pin]
 pin: PC4
 pwm: True
 value: 0
 shutdown_value: 0
 cycle_time: 0.001
 
#Dual Extruder Stuff
[gcode_macro T0]
 #Macro to run when switching to main extruder
 gcode:
    SET_GCODE_OFFSET X=0                        #Clear X offset
    ACTIVATE_EXTRUDER EXTRUDER=extruder
	
[gcode_macro T1]
 #Macro to run when switching to second extruder
 gcode:
    SET_GCODE_OFFSET X=55                       #Nozzle 2 is offset by 55mm in X from nozzle 1
    ACTIVATE_EXTRUDER EXTRUDER=extruder1
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

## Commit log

2026-01-11 Add base klipper config file
    [base-config.cfg]
2026-02-01 Add part files for XY upright
    [GB3+ XY Upright - Modified.SLDPRT, GB3+ XY Upright - Modified.STEP]
2026-02-01 Create Optical Endstop V1.zip
2026-02-01 Add 3D files for optical endstop mod.
    [Motor Mount - Modified.SLDPRT, Motor Mount - Modified.STEP, Motor Mount - Modified.STL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]
2026-02-02 Add PCB layout pictures
2026-02-10 Add TC case models
    [Thermocouple Conditioner Case Top.SLDPRT, Thermocouple Conditioner Case Top.STEP, Thermocouple Conditioner Case Top.STL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]
